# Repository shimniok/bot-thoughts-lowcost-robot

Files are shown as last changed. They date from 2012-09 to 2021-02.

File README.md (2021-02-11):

# bot-thoughts-lowcost-robot

Entry for 2012 African Robotics Network Challenge to build a $10, educational robot.



[Bot Thoughts Blog article](https://www.bot-thoughts.com/2012/09/entry-for-afron-10-dollar-robot-design.html)

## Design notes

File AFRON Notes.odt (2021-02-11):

Main issues:

Board assembly astronomically expensive, PTH self assembly may be the only option here. Even so have to have some level of SMT assembly for the motor drivers.

Servo work on 2xAA ? (2v – 3V) ? 3V=Yes, 2V=Untested

LiPo or AA (Alkaline or NiMH)?

Where to mount battery?

Ongoing cost of batteries (AA's are cheap but... not renewable)

Where to put sensors? Separate board = more $, mounting?? – chassis-board may be best?

3rd wheel steer bracket?

I don't have motor drivers prototyped

All the little extras are “nickle and dime”-ing this thing to $30

Test MiniBloq on 8mhz version

I'm out of money and time :)

Resolved

Will servo work on Lipo? ~3.7V? YES

Prototyped Arduino at Lipo/AA power, 4MHz (could do 8mhz with LiPo)

On-board LiPo charger or off-board? Off-board, but motor system could be its own charger; need to redirect power to charger board somehow.

On-board USB or off-board? (off-board, but could have ftdi / AVRISP shield and later revision could use mega32u4

AA requires 4MHz (5.333MHz @ 2V, 6.6667MHz @ 2.2V, 8MHz @ 2.4V)

LiPo can do 8MHz; change of MHz requires change to bootloader (can I get around this?)

Cost of wheels – Options: cardboard, bottle tops, cheap toy wheels

I don't have minibloq software going

I don't actually have the designed motor/gearbox yet

Features

Stackable headers for shields. Small size shields for low cost diy, hacking, low cost shield options for expanding capabilities

Built-in LEDs/Phototrans/Sensors can be disabled for use with shield

DIY solder assembly, secondary students can assemble for primary; benefit of lower cost plus gaining education (at some point you run out of people to pass robots down to though)

Arduino compatible

With booster circuit, can run with MiniBloq, either on regular laptop or OLPC laptop

Assembly Instructions

Summary

Highlights of board, features

Online documentation

Disable all phototransistor/LEDs : cut the power trace

Disable individual phototrans pins but cutting those traces

Support AA or 3.7V 1S Lipo?!

1. A high-level description of your robot design with total cost (for one prototype unit; see point 7

regarding volume pricing).

• Include in your description an indication of whether your robot is designed to be built from

scratch by the user, or mass manufactured and supplied as a kit to the user

• Some robots might have required accessories (e.g. a tool for downloading programs to the

robot) that can be shared by multiple robots in a classroom. If applicable, include such a

tool in the cost for a single robot, but also specify whether it can be shared by multiple

robots, thus bringing down the overall deployment cost for a classroom.

2. A description of the educational applications and possible resources.

• For example, what science and technology concepts or skills can your robot help students

learn?

3. A list of parts, their sources (include URLs if applicable), availability, and their prices.

• Note that salvaged parts are allowed, if these salvaged parts are commonly available in

your particular context. Think of this list of parts as the starting point if someone in a

similar context to you wanted to reproduce your robot.

• Note also that your parts list should be complete, including things like required adhesive,

screws etc.

• Your parts list should include any consumables (e.g. batteries) and their associated cost

and replacement frequency. This is a caution to think of sustainability.

4. A list of other tools and equipment needed to create your robot and estimated prices

5. Relevant drawings with dimensions.

• These may be CAD drawings, particularly for machined parts, but they may also be hand-

drawn

6. Step-by-step instructions for creating your robot

7. [Optional] If your robot can be mass manufactured, you can present an analysis of how costs

would scale with quantity.

8. Software, if any. All software must be available open-source.

9. A description of any actual experiments conducted

10. Pictures of your robot, if any.

11. Videos of your robot in action, if any.

• These videos should highlight key capabilities such as its ability to respond autonomously

to its environment.

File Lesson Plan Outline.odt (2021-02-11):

Robotics Lesson Plan Outline

I. Basic Electronics and Switches
  A. Electricity intro
    i. Batteries
    ii. Circuit
    iii. LED
    iv. Switch(?)
    v. Resistor(?)
  B. (Opt.) Solder components on board (assembled robots to primary edu)
  C. Wire up sensor switch(?)
  D. Load demo program (light LED when switch closed)
II. Motors and gears
  A. Force and Distance
    i. Leverage
    ii. Pulleys
  B. Gear reduction
    i. Leverage, torque
    ii. RPM, Formulas
      a. Calculate for our robot
    iii. Load demo motor driver
      a. RPM with motor out of case
      b. Demo wheel rpm with motor in
III. Simple programming with Minibloq
  A. Turn on LED
  B. Turn on LED with switch(?)
IV. Line following with Infrared Light
  A. Light spectrum
  B. Infrared light
  C. LED review
  D. Phototransistors

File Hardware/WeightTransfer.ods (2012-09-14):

AFRON ROBOT WEIGHT TRANSFER DATA
Inner | Outer | Total | Inner % | Outer %
28 | 34 | 62 | 45% | 55%
22 | 38 | 60 | 37% | 63%
20 | 40 | 60 | 33% | 67%
26 | 38 | 64 | 41% | 59%

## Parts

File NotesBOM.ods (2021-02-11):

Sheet: Sheet1
Mass Production Cost Analysis
Summary | Description | Price ($) / Pack | Qty / Pack | Qty / Robot | Packs / 1000 | Subtotal @ 1000 | Price Ea. @ 1000 | Source
Locomotion
Gearbox | UCTronics 6V Dual axle brush DC Gear Motor & boxes | 2.9 | 1 | 1 | 1000 | $2,900.00 | $2.90
Drive wheels | 20x8x2 | 26.32 | 100 | 2 | 20 | $526.40 | $0.26 | http://www.aliexpress.com/item/20x8x2mm-Academic-Model-Small-Wheels-Plastic-DIY-Toys-Hobbies-Parts-and-Accessories/517602128.html
Axles | 2mm x 20mm axle | 7.59 | 80 | 2 | 25 | $189.75 | $0.09 | http://www.aliexpress.com/item/20mm-2mm-Toys-axle-Shaft-axis/582061924.html
Rear steer wheels | Fingerboard wheels (400 pack) | 20 | 400 | 2 | 5 | $100.00 | $0.05 | http://www.aliexpress.com/item/400pcs-10-Colors-Wheel-For-Fingerboard-Mini-Skateboard-Finger-board/447293443.html
Rear steer bracket | Fingerboard Truck, screws, nuts, red | 80 | 200 | 1 | 5 | $400.00 | $0.40 | http://www.aliexpress.com/item/wholesale-200pcs-finger-skateboard-truck-fingerboards-truck-29-mm-wide-truck-fee-shipping-by-UPS-EMS/446988459.html
Bracket | Servo mount bracket | 0.03 | 1 | 1 | 1000 | $30.00 | $0.03 | http://www.cshardware.com/steel-brackets/15-3412.asp
Servo | TowerPro SG90, 9g servo | 177.38 | 100 | 1 | 10 | $1,773.80 | $1.77 | http://www.aliexpress.com/item/fast-shipping-100pcs-Tower-Pro-9g-micro-servo-for-6CH-rc-helcopter-kds-esky-align-helicopter/555525944.html
Sensors
3mm 940nm IR LED | Kingbright WP710A10F3C | 0.104 | 1 | 4 | 4000 | $416.00 | $0.10 | Digi-Key
3mm 940nm IR PhotoTrans | LTR-4206E | 0.09 | 1 | 4 | 4000 | $360.00 | $0.09 | Digi-Key
Heat Shrink | HEATSHRINK LOW TEMP 1/8" 60' BLK | 23.18 | 720 | 3 | 5 | $115.90 | $0.04 | Digi-Key
Main Board
MCU | ATmega328P-PU | 1.7628 | 1 | 1 | 1000 | $1,762.80 | $1.76 | Digi-Key
Driver IC | SI1563EDH-T1-E3 1.8V SOT-363 | 0.1919 | 1 | 2 | 2000 | $383.80 | $0.19 | Digi-Key
Crystal resonator | Murata CSTLS8M00G53-B0 | 0.1234 | 1 | 1 | 1000 | $123.42 | $0.12 | Digi-Key
LED | 3mm LED, water clear, green | 0.0481 | 1 | 1 | 1000 | $48.10 | $0.05 | Digi-Key
Motor capacitor | Vishay K103K10X7RF5UH5, CAP CER 10000PF 50V 10% RADIAL | 0.0303 | 1 | 1 | 1000 | $30.30 | $0.03 | Digi-Key
0.1uF Bypass capacitor | Vishay K104K10X7RF5UH5, CAP CER 0.1UF 50V 10% RADIAL | 0.0369 | 1 | 3 | 3000 | $110.70 | $0.04 | Digi-Key
100uF capacitor | Kemet ESK107M010AC3AA | 0.02954 | 1 | 1 | 1000 | $29.54 | $0.03 | Digi-Key
100 ohm resistor | Stackpole CF18JT100R | 0.00992 | 1 | 5
Description | Price @ 1 | Price @ 100 | Price @ 1000 | Qty | Subtotal | Option 1 | Option 2 | Option 2 | Option 3 | Drivetrain
UCTronics 6V Dual axle brush DC Gear Motor & boxes | $2.90 |  |  | 1 | $2.90 | $2.90 | $2.90 | $2.90
Dollar store | $1.00 | $1.00 | $1.00 | 1 | $1.00 | $1.00
CDR for wheel | $0.16 | $0.16 | $0.16 | 2 | $0.32 |  |  | $0.32
AliExpress | $0.44 | $0.40 | $0.40 | 2 | $0.88 |  | $0.88
AliExpress | $0.40 | $0.36 | $0.36 | 1 | $0.40 |  | $0.40
K&S, 2mm dia, unknown length, 4-pack | $1.79 |  |  | 1 | $1.79
FDS9934C 6.5A/-5A SO-8 | $0.91 | $0.61 | $0.36 | 2 | $1.82 | $1.82 | $1.82 | $1.82
20-pack | $0.59 | $0.59 | $0.59 | 1 | $0.59 |  |  |  | $0.59
Woodwoorks 1" bead | $0.20 | $0.20 | $0.20 | 2 | $0.40 |  |  |  | $0.40
Woodworks 3/8" hardwood dowel | $1.19 | $1.19 | $1.19 | 1 | $1.19 |  |  |  | $0.50
EXI S1123 9G Micro Servo | $3.00 |  |  | 1 | $3.00 | $3.00 | $3.00 | $3.00 | $3.00
 |  |  |  |  |  | $8.72 | $9.00 | $8.04 | $4.49 | TOTALS
 |  |  |  |  |  |  |  |  |  | Sensors
 | $0.87 | $0.58 | $0.43 | 2 | $1.74 |  |  | $1.74
 | $0.93 |  |  | 2 | $1.86 |  |  |  | $1.86
 | $0.26 | $0.14 | $0.10 | 3 | $0.78 | $0.78 | $0.78
 | $0.38 | $0.18 | $0.09 | 3 | $1.14 | $1.14
Vishay TSOP34838 | $1.14 |  |  | 1 | $1.14 |  | $1.14
K&S 0.015 25pk | $0.42 |  |  | 1 | $0.42 | $0.42 | $0.42 | $0.42
 |  |  |  |  |  | $1.92 | $1.92 | $1.74 | $1.86 | TOTALS
 |  |  |  |  |  |  |  |  |  | MCU, board, USB, Batt
Digikey price | $1.92 | $1.35 | $1.20 | 1 | $1.92
Appx price | $1.20 | $0.76 | $0.67 | 1 | $1.20 |  |  |  | $1.20
Appx price | $3.50 |  |  | 1 | $3.50
Appx price | $3.05 | $1.92 | $1.70 | 1 | $3.05 | $3.05 |  |  |  |  | Note: MiniBloq only supports ATmega328/168 and ATtiny25/45/85
Digikey | $6.04 | $3.37 | $3.37 | 1 | $6.04 |  |  | $6.04
Appx price | $3.80 |  |  | 1 | $3.80 |  | $3.80
FTDI chip (digikey) | $2.38 | $1.79 | $1.58 | 1 | $2.38 | $2.38 |  |  | $2.38
FT232RL, Digikey | $4.50 | $3.65 | $2.85 | 1 | $4.50
digikey | $0.68 | $0.55 | $0.55 | 1 | $0.68 | $0.68 | $0.68 | $0.68 | $0.68
3 x 3mm / #2
Sparkfun | $18.00 |  |  | 1 | $18.00
various sources | $3.00 |  |  | 1 | $3.00 | $3.00 | $3.00 | $3.00 | $3.00
SFE | $10.00
asdf | $0.15 | $0.10 | $0.08 | 2 | $0.30 | $0.30 | $0.30 | $0.30 | $0.30
Lipo, 1S, 210mAH 15C | $1.77 |  |  | 1 | $1.77
 |  |  |  |  |  | $9.41 | $7.78 | $10.02 | $7.56 | TOTALS
 |  |  |  |  |  |  |  | $20.05 |  | TOTALS
LB1836M; 1.8V motor, 2.5V logic, 1A | $4.61 |  |  | 1 | $4.61
sn754410 appx price | $2.30 |  |  | 1 | $2.30
4.5V-18V TC4427A appx price | $1.50 |  |  | 1 | $1.50
Victor mousetrap, amazon, 4-pack | $1.16 |  |  | 2 | $2.32
72-pack | $0.54 |  |  | 72 | $38.95
20-pack | $0.59 |  |  | 20 | $11.78
Car Robot Plastic Tire Wheel + DC Gear Motor (ebay) | $4.19 |  |  | 2 | $8.38
Car Robot Plastic Tire Wheel + DC Gear Motor (ebay) | $2.95 | $2.95 | $2.95 | 2 | $5.90
11 pc plastic | $2.50 |  |  | 1 | $2.50
1230 Mini Hi Torque motor | $1.70 |  |  | 2 | $3.40
Woodworks 2.5" flat wood wheel | $0.58 |  |  | 2 | $1.15
Woodwoorks 1" bead | $0.20 |  |  | 2 | $0.40
Woodworks 2" flat wood wheel | $0.30 |  |  | 2 | $0.60 |  |  |  | $0.60
Surplus Elect Sales 3V hobby motor | $0.99 |  |  | 1 | $0.99
5V 7200 rpm dc motor | $0.65 |  |  | 2 | $1.30
ULTRALAST UL40AAVP 40-pack AA Alkaline Batteries (newegg) | $0.22 |  |  | 2 | $0.45
AA, cheapbatteries.com | $0.15 | $0.10 | $0.08 | 2 | $0.30
LB1838M, stepper only? low voltage | $3.11 |  |  | 1 | $3.11
BD6211 8SOIC | $3.24 |  |  | 1 | $3.24
DRV8830, 10MSOP | $2.71 |  |  | 1 | $2.71
ZXMHC3F381 H-bridge | $1.08 |  |  | 1 | $1.08
4.5V+ (see Pololu Baby-O 328P, only carried at DigiKey) | $2.03 |  |  | 1 | $2.03 |  |  | $2.03 | $2.03
DRV8837, single H-bridge, DSG pkg | $1.62 | $1.13 | $0.70 | 1 | $1.62 | $1.62 | $1.62
2V - 11V; See Pololu DRV8835; Ti part, DigiKey best price; DFN pkg | $2.23 | $1.62 | $1.04 | 1 | $2.23 |  | $2.23
DigiKey | $1.94 | $1.08 | $1.08
DigiKey (appx) | $4.80
Pair | $9.95
FDC6327C 2.5V 2.7A/-1.9A SOT-6 | $0.51 | $0.32 | $0.18 | 2 | $1.02
SI1563EDH-T1-E3 1.8V SOT-363 | $0.56 | $0.33 | $0.19 | 2 | $1.12
NTHC5513 3.9A/-3.0A ChipFET | $0.64 | $0.40 | $0.23 | 2 | $1.28
NTHD3102CT 5.5A/-4.2A ChipFET | $0.68 | $0.46 | $0.27 | 2 | $1.36
SI519EDJ 4.5A/-4.5A PowerPak 8 | $0.74 | $0.45 | $0.26 | 2 | $1.48
Si3590DV 2A/-1.3A TSOP-6 | $0.79 | $0.48 | $0.27 | 2 | $1.58
DMC2020USD 7.8A/-6.3A SO-8 | $0.82 | $0.56 | $0.33 | 2 | $1.64
FDS9934C 6.5A/-5A SO-8 | $0.91 | $0.61 | $0.36 | 2 | $1.82 | $1.82 | $1.82 | $1.82
NTHD3102CT 5.5A/-4.2A ChipFET | $0.68 | $0.46 | $0.27 | 2 | $1.36 | $1.36 | $1.36 | $1.36
SFE | $10.00
SFE | $14.95
various | $3.00
 | $3.30 |  |  |  |  |  |  |  |  |  | http://www.aliexpress.com/item/20W-110V-220V-Mini-Electric-Heating-Hot-Melt-Glue-Gun-Crafts-Repair-Tool-Professional-US-Plug/487529881.html
 | $0.18 |  |  |  |  |  |  |  |  |  | http://www.aliexpress.com/item/free-shipping-7-100mm-Home-essential-universal-hot-melt-tape-hot-melt-glue-stick-100pcs-alot/607201791.html
PCBFabExpress |  | $25.70 | $18.75 |  |  |  |  |  |  |  | http://www.pcbfabexpress.com/assembly/as_quotemain_test.jsp
Screaming Circuits |  | $19.31 | $18.82 |  |  |  |  |  |  |  | http://www.screamingcircuits.com
MyroPCB |  | $3.53 |  |  |  |  |  |  |  |  | http://www.myropcb.com/online-quote/pcba-prototype-quote/
Hakko 503F-V12ED 60 Watt Heavy Duty Solder Iron | $11.92 |  |  |  |  |  |  |  |  |  | http://www.frys.com/product/249084?source=googleps&gclid=CKK6hK3Dq7ICFSVgMgod-2UAXQ
Weller SP23L 25 Watt Marksman Solder Iron | $9.97 |  |  |  |  |  |  |  |  |  | http://www.frys.com/product/2818734?site=sr:SEARCH:MAIN_RSLT_PG
220V 60W | $6.88 |  |  |  |  |  |  |  |  |  | http://www.ebay.com/itm/AC-220V-40-Watt-Soldering-Iron-Dissolved-solder-Tip-Electronic-Welding-TOOL-/140811445683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
220V 40W | $3.20 |  |  |  |  |  |  |  |  |  | http://www.aliexpress.com/item/Fast-Heating-Welding-Soldering-Iron-Tool-Electronic-PC-40W-220V-SHT-0075/622355190.html
110/220 25W-60W | $14.99 |  |  |  |  |  |  |  |  |  | http://www.aliexpress.com/item/110V-220V-Adjustable-Gun-Welding-Soldering-Solder-Iron-Handle-Tool-For-933-Station-Heat-Pencil-25W/572357938.html
FEITA 30W 40W 60W 80W electric solder Irons with ROHS SGS | $5.85 |  |  |  |  |  |  |  |  |  | http://www.aliexpress.com/item/30W-40W-60W-80W-electric-welder-Irons/434076066.html

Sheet: Sheet2
 |  |  |  |  |  | http://www.aliexpress.com/item/4-5-inch-besk-pliers-VK-031/460402968.html
Steer Wheel Bracket | Brass, e-machine shop | $1.92 |  | $1.96 | $1.06
Steer Wheel Bracket | inj molded nylon | $1.04 |  | $4.74 | $1.04
Steer Wheel Bracket | 5/8" square bead, 1/4" hole | $0.11 | 1 | $0.11 | $0.08 | http://www.craftparts.com/square-beads-hole-p-1018.html
Steer Wheel | 1" wood slab wheel | $0.15 | 2 | $0.15 | $0.12 | http://www.craftparts.com/flat-wood-slab-wheels-thick-p-590.html
Steer axle | 1-3/8" x 1/4" peg | $0.05 | 2 | $0.09 | $0.08 | http://www.craftparts.com/138-axle-pegs-1564-tenon-p-851.html
Steer Wheel | dia unknown | $0.27 |  |  |  | http://www.aliexpress.com/item/100pcs-DIY-accessories-Plastic-toy-car-wheels-3CM/450620588.html
Wheel | 30x9x1.9 | $0.70 |  | $0.60 |  | http://www.aliexpress.com/item/Free-shipping-30-9-1-9mm-Plastic-wheel-DIY-handmade-Model-accessories-Toy-car-wheels/574791665.html
Wheel | 18x6.5x2 | $0.34 |  | $0.34 | $0.30 | http://www.aliexpress.com/item/18x6-5x2mm-Academic-Model-Small-Plastic-Toy-Car-Wheels-DIY-Hobbies-Parts-and-Accessories/517605266.html
Wheel | 20x8x2 | $0.29 |  |  |  | http://www.aliexpress.com/item/20x8x2mm-Academic-Model-Small-Wheels-Plastic-DIY-Toys-Hobbies-Parts-and-Accessories/517602128.html
Wheel (clear) | 64x2.5mm | $0.56 |  |  |  | http://www.aliexpress.com/item/30pcs-DIY-Accessories-Plastic-toy-car-wheels-64MM-Remote-control-car-wheels/452423232.html
Wheel | 46x22x2 | $0.29 |  |  |  | http://www.aliexpress.com/item/50pcs-DIY-accessories-Plastic-toy-car-wheels-4-6CM/450625545.html
Wheel | 45x18x3 | $0.45 |  |  |  | http://www.aliexpress.com/item/45x18x3mm-Academic-Model-Small-Wheels-Plastic-DIY-Toys-Hobbies-Parts-and-Accessories/517593841.html
Wheel | 58x2.5 | $0.69 |  |  |  | http://www.aliexpress.com/item/toy-wheels-58mm-plastic-wheels-Shaft-Diameter-2-5mm-model-making-DIY-model-accessories-10-pcs/573590653.html
42mm Tires/Wheels 2mm | AliExpress | $0.19 | 3 | $0.57 | $0.57 | http://www.aliexpress.com/item/Free-Sipping-Toy-plastic-wheel-Technology-Small-Productions-DIY-Accessories-30mm-diameter-hole-2mm/591272358.html
Rear steer wheel | Fingerboard wheels (400) | $0.05 | 2 | $0.10 | $0.10 | http://www.aliexpress.com/item/400pcs-10-Colors-Wheel-For-Fingerboard-Mini-Skateboard-Finger-board/447293443.html
Rear steer wheel | Fingerboard bearing wheels | $0.24 | 2 | $0.48 | $0.48 | http://www.aliexpress.com/item/fingerboards-bearing-wheel-bearing-wheels-finger-skateboard-bearing-wheel-free-shipping/447735920.html
Rear steer bracket | Fingerboard Truck, screws, nuts, red | $0.43 | 1 | $0.43 | $0.43 | http://www.aliexpress.com/item/wholesale-200pcs-finger-skateboard-truck-fingerboards-truck-29-mm-wide-truck-fee-shipping-by-UPS-EMS/446988459.html
Bracket | Servo mount bracket | $0.05 | 1 | $0.05 | $0.05 | http://www.cshardware.com/steel-brackets/15-3412.asp
Steer wheel bracket | Wood square dowel | $0.32 | 1 | $0.32 | $0.32
Steer bracket, wheel | truck, wheels, nuts | $0.45 | 1 | $0.45 | $0.45 | http://www.ebay.com/itm/20-Trucks-40-Wheels-For-96mm-Fingerboard-Skateboard-Canadian-Maple-wooden-M19E-/110947473210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
2mm x 30mm axle | AliExpress | $0.20 | 1 | $0.20 | $0.20 | http://www.aliexpress.com/item/30mm-2mm-Toys-axle-Shaft-axis/582062768.html

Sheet: Sheet3
Drive axles | 2mm x 20mm axle | $0.20 | 2 | $0.40 | http://www.aliexpress.com/item/20mm-2mm-Toys-axle-Shaft-axis/582061924.html
Drive wheels | 20x8x2 | $0.29 | 2 | $0.58 | http://www.aliexpress.com/item/20x8x2mm-Academic-Model-Small-Wheels-Plastic-DIY-Toys-Hobbies-Parts-and-Accessories/517602128.html
Servo | AliExpress, bulk or HobbyPartz, one | $3.00 | 1 | $3.00 | http://www.aliexpress.com/item/fast-shipping-100pcs-Tower-Pro-9g-micro-servo-for-6CH-rc-helcopter-kds-esky-align-helicopter/555525944.html
 | UCTronics 6V Dual axle brush DC Gear Motor & boxes
Rear steer wheels | Fingerboard wheels (400) | $0.05 | 2 | $0.10 | http://www.aliexpress.com/item/400pcs-10-Colors-Wheel-For-Fingerboard-Mini-Skateboard-Finger-board/447293443.html
Rear steer bracket | Fingerboard Truck, screws, nuts, red | $0.43 | 1 | $0.43 | http://www.aliexpress.com/item/wholesale-200pcs-finger-skateboard-truck-fingerboards-truck-29-mm-wide-truck-fee-shipping-by-UPS-EMS/446988459.html
100 resistor | 1/8W similar to Stackpole CF18JT100R | $0.09 | 4 | $0.36
1K resistor | 1/8W similar to Stackpole CF18JT1K00 | $0.09 | 1 | $0.09
10K resistor | 1/8W similar to Stackpole CF18JT1M00 | $0.09 | 7 | $0.63
Motor driver | SI1563EDH-T1-E3 1.8V SOT-363 | $0.56 | 2 | $1.12
Motor Driver IC | Pololu DRV8835 breakout | $5.95 | 1 | $5.95
Charger |  | 9.95 |  |  | https://www.sparkfun.com/products/10217
Production battery | 3.7V 1S 600mAH, 2-pin JST | 2.73 |  |  | http://www.hobbyking.com/hobbyking/store/__20385__Turnigy_nano_tech_600mah_1S_35_70C_Lipo_Pack_Fits_Nine_Eagles_Solo_Pro_328_Eflite_MQX_120SR_.html
Production battery | 3.7V 1S 750mAH, 2-pin molex | 2.34 |  |  | http://www.hobbyking.com/hobbyking/store/__20386__Turnigy_nano_tech_750mah_1S_35_70C_Lipo_Pack_Fits_Nine_Eagles_Solo_Pro_180_.html

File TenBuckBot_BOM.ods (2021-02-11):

10 Dollar Robot Design Challenge
Bill of Materials
Prototype
Chassis |  | Qty 1
Wheels | Dollar store pull-back toy car | $1.00
Axles | See wheels
Chassis platform | Scrap cardboard | $0.00
Wood glue
Drive system | Solarbotics single-motor, dual axle gearbox | $5.95
Steering servo | EX1123 Servo | $3.00
Electronics
MCU | ATmega328P
Passives
Connectors
Sensors | 3 x IR LED |  |  | 3 x IR LED
 | 3 x IR Phototransistor |  |  | 3 x IR Phototransistor
Battery
Battery holder
Board | Assembly
 | Population
Accessories and Tools
programmer | FTDI breakout | $14.95 |  | FTDI cable (one per classroom) | $18.00
 | USB Cable | $3.00
Mass Produced Kit
 | Qty 1 | Qty 100 | Qty 1000
Scrap bottle tops, cardboard, CDs | $0.00 | $0.00 | $0.00
95mm x 2mm (AliExpress) | $0.40 | $0.36
Scrap cardboard, coke can, etc. | $0.00 | $0.00 | $0.00
UCTronics single-motor, dual axle gearbox | $2.90
Any 9g servo | $3.00
AliExpress: TP SG90 |  | $1.94

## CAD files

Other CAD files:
Electronics/AFRON_328_chassis.skp
Hardware/18mm Wheel.skp
Hardware/30mm Wheel.skp
Hardware/42mm Wheel.skp
Hardware/AFRON_Board.skp
Hardware/AFRON_Line_Sensor.skp
Hardware/Fingerboard.skp
Hardware/FingerboardRearSteer.skp
Hardware/PlasticServoMount.skp
Hardware/Servo Tower Pro Micro SG-90 with horns.skp
Hardware/SteerBracket.skp
Hardware/WoodPulley.skp
Hardware/WoodRearSteer.skp

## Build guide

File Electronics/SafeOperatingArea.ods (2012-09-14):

Clock | Clkdiv | Timer clock | OCR | Interrupt freq | Duty counter | PWM freq
8.00E+006 | 1 | 8000000 | 20 | 400000 | 64 | 6250
 |  |  |  | 5.00%
ATmega328P Safe Operating Area
rise | 4 | 10 | 6
run | 1.8 | 2.7 | 0.9 |  |  | V | F | rise | run | rise/run | Y-intercept
 |  |  | 6.6666666667 |  |  | 1.8 | 4
Volt | MHz |  |  |  |  | 2.7 | 10 | 6 | 0.9 | 6.6666666667 | -8
1.8 | 4.0 |  |  |  |  | 4.5 | 20 | 10 | 1.8 | 5.5555555556 | -5
1.9 | 4.7
2.0 | 5.3 |  | 4.5
2.1 | 6.0
2.2 | 6.7
2.3 | 7.3
2.4 | 8.0
2.5 | 8.7
2.6 | 9.3
2.7 | 10.0
2.8 | 10.6
2.9 | 11.1
3.0 | 11.7
3.1 | 12.2
3.2 | 12.8
3.3 | 13.3
3.4 | 13.9
3.5 | 14.4
3.6 | 15.0
3.7 | 15.6
3.8 | 16.0
3.9 | 16.7
4.0 | 17.2
4.1 | 17.8
4.2 | 18.3
4.3 | 18.9
4.4 | 19.4
4.5 | 20.0

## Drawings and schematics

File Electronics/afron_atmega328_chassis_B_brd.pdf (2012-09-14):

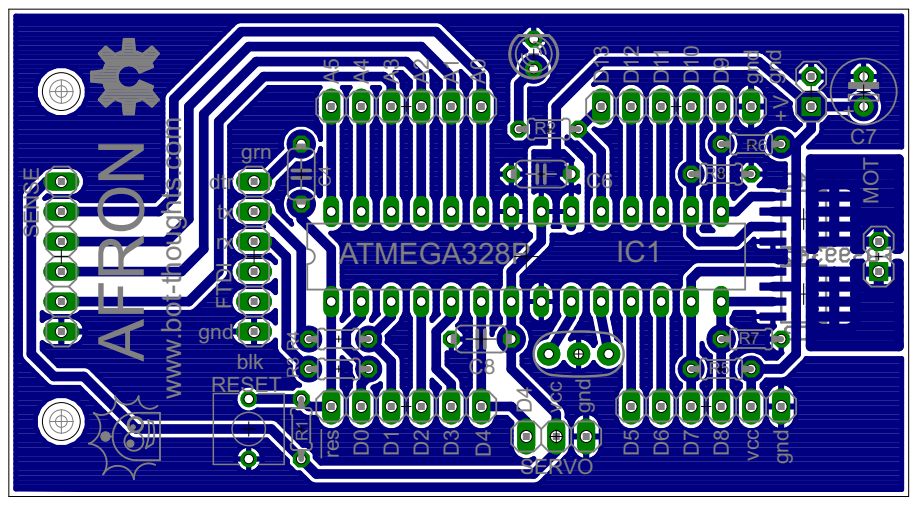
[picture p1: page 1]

AFRON www.bot-thoughts.com A3A4A5 vcc D2D3 gnd D4 vcc gnd D5D6 D11 D12 gnddtrtxrx A2A1A0 D7D8 D10 D9 D1D0 D13 RESET blkgrn D4 gnd res gnd R1 C6 R2 C4 R3 R4 R5 R6 R7 R8 IC1 C8 C7 +V FTDIATMEGA328P MOT SENSE SERVO

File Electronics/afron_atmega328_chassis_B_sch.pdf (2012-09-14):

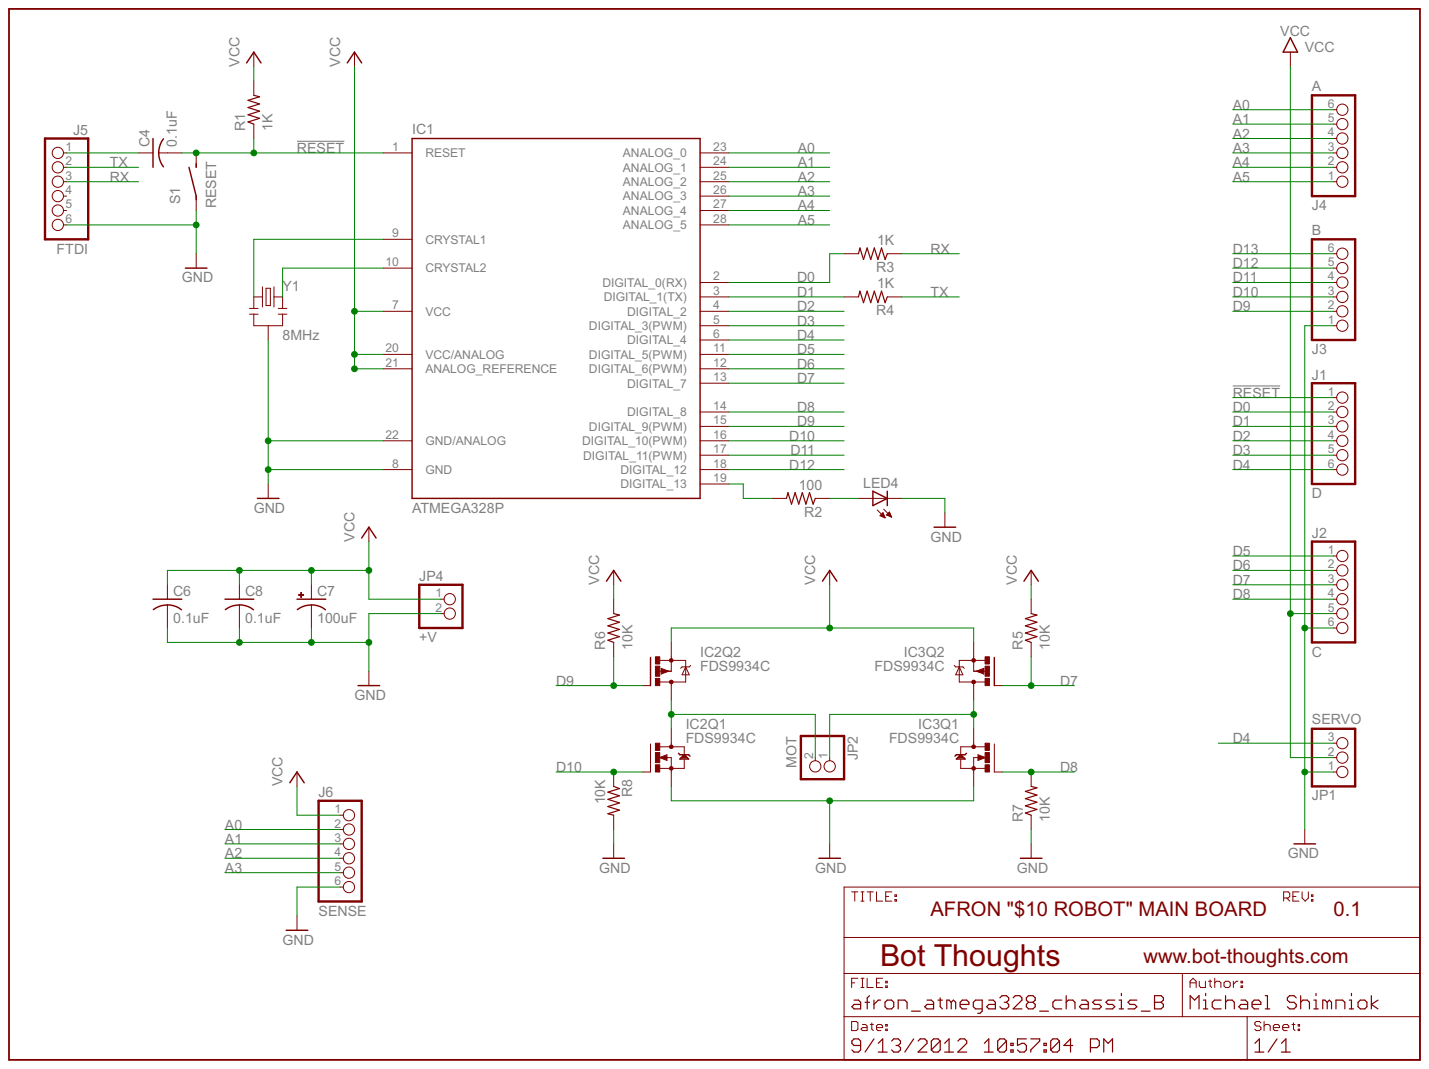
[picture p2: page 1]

20 | | 6 DIGITAL_3(PWM) 5 DIGITAL_2 D3

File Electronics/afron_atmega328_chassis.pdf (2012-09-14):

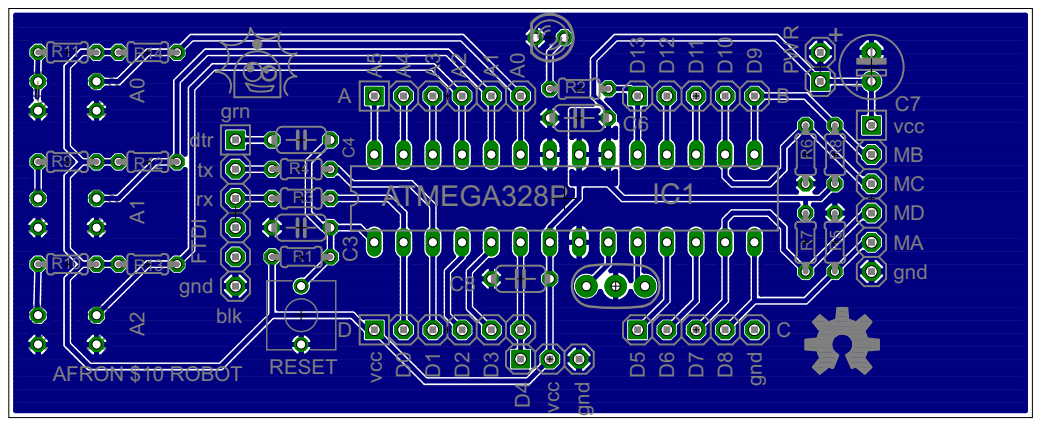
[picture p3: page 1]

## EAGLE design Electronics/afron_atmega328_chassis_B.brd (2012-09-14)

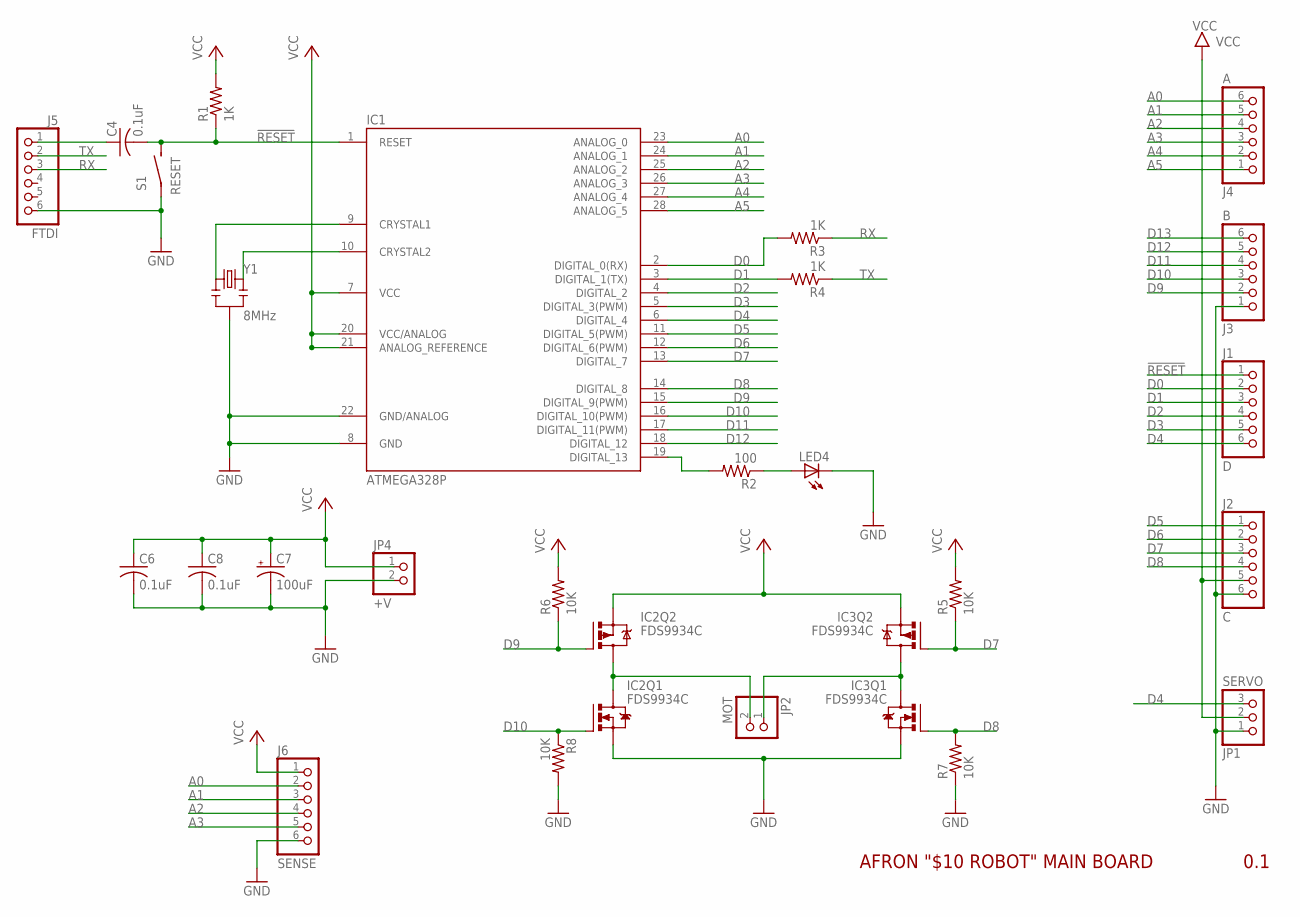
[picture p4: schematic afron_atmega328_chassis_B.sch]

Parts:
C4, C6, C8: 0.1uF; C050-024X044
C7: 100uF; E2,5-6
IC1: ATMEGA328P; DIL28-3
IC2, IC3: FDS9934C; SOIC8
J1: D; 1X06
J2: C; 1X06
J3: B; 1X06
J4: A; 1X06
J5: FTDI; 1X06
J6: SENSE; 1X06
JP1: SERVO; 1X03
JP2: MOT; 1X02-S
JP4: +V; 1X02-S
LED4: LED3MM
R1, R3, R4: 1K; 0204/5
R2: 100; 0204/5
R5, R6, R7, R8: 10K; 0204/5
S1: RESET; 6MMTACTILE
Y1: 8MHz; RESONATOR-PTH

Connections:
!RESET: C4.2, IC1.1 (RESET), J1.1, R1.1, S1.P$2 (S)
A0: IC1.23 (ANALOG_0), J4.6, J6.2
A1: IC1.24 (ANALOG_1), J4.5, J6.3
A2: IC1.25 (ANALOG_2), J4.4, J6.4
A3: IC1.26 (ANALOG_3), J4.3, J6.5
A4: IC1.27 (ANALOG_4), J4.2
A5: IC1.28 (ANALOG_5), J4.1
D0: IC1.2 (DIGITAL_0(RX)), J1.2, R3.2
D1: IC1.3 (DIGITAL_1(TX)), J1.3, R4.2
D2: IC1.4 (DIGITAL_2), J1.4
D3: IC1.5 (DIGITAL_3(PWM)), J1.5
D4: IC1.6 (DIGITAL_4), J1.6, JP1.3
D5: IC1.11 (DIGITAL_5(PWM)), J2.1
D6: IC1.12 (DIGITAL_6(PWM)), J2.2
D7: IC1.13 (DIGITAL_7), IC3.4 (G), J2.3, R5.1
D8: IC1.14 (DIGITAL_8), IC3.2 (G), J2.4, R7.2
D9: IC1.15 (DIGITAL_9(PWM)), IC2.4 (G), J3.2, R6.1
D10: IC1.16 (DIGITAL_10(PWM)), IC2.2 (G), J3.3, R8.1
D11: IC1.17 (DIGITAL_11(PWM)), J3.4
D12: IC1.18 (DIGITAL_12), J3.5
D13: IC1.19 (DIGITAL_13), J3.6, R2.2
GND: C6.2, C7.-, C8.2, IC1.8 (GND), IC1.22 (GND/ANALOG), IC2.1 (S), IC3.1 (S), J2.6, J3.1, J5.6, J6.6, JP1.1, JP4.2, LED4.K (C), R7.1, R8.2, S1.P$1, Y1.2
MA: IC2.5 (D), IC2.6 (D), IC2.7 (D), IC2.8 (D), JP2.2
MB: IC3.5 (D), IC3.6 (D), IC3.7 (D), IC3.8 (D), JP2.1
unnamed: IC1.9 (CRYSTAL1), Y1.1
unnamed: IC1.10 (CRYSTAL2), Y1.3
unnamed: C4.1, J5.1
unnamed: LED4.A, R2.1
RX: J5.3, R3.1
TX: J5.2, R4.1
VCC: C6.1, C7.+, C8.1, IC1.7 (VCC), IC1.20 (VCC/ANALOG), IC1.21 (ANALOG_REFERENCE), IC2.3 (S), IC3.3 (S), J2.5, J6.1, JP1.2, JP4.1, R1.2, R5.2, R6.2

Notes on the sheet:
AFRON "$10 ROBOT" MAIN BOARD
0.1

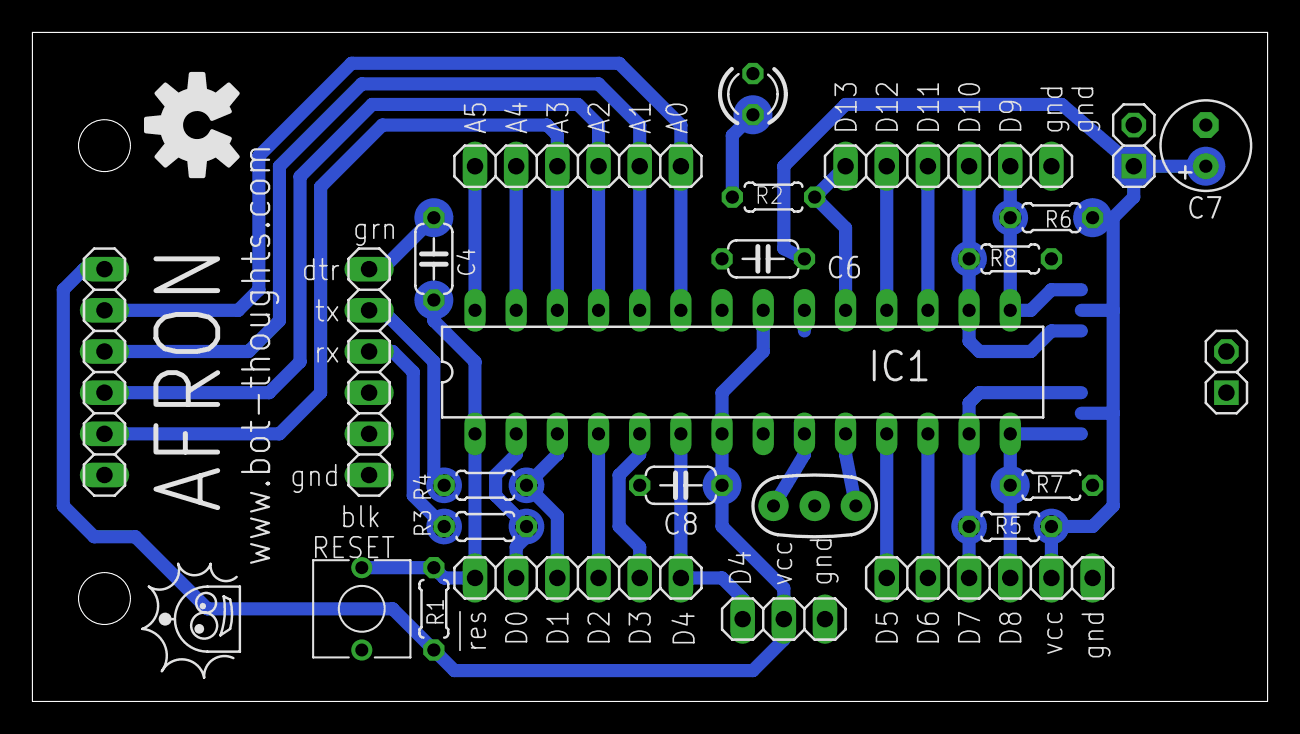
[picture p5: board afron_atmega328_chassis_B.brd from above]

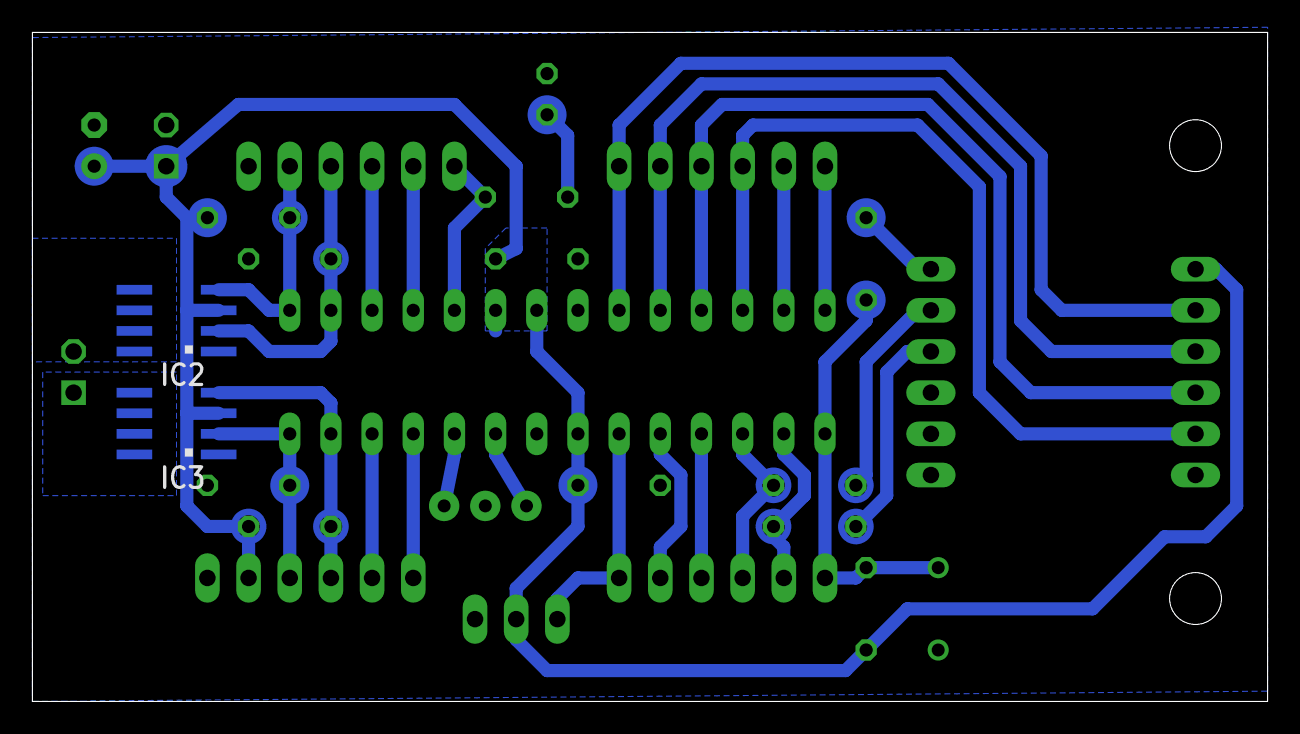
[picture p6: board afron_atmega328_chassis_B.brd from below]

Board: 2 copper layers, 76.2 x 41.3 mm, 27 parts (2 on the bottom side), 31 nets.

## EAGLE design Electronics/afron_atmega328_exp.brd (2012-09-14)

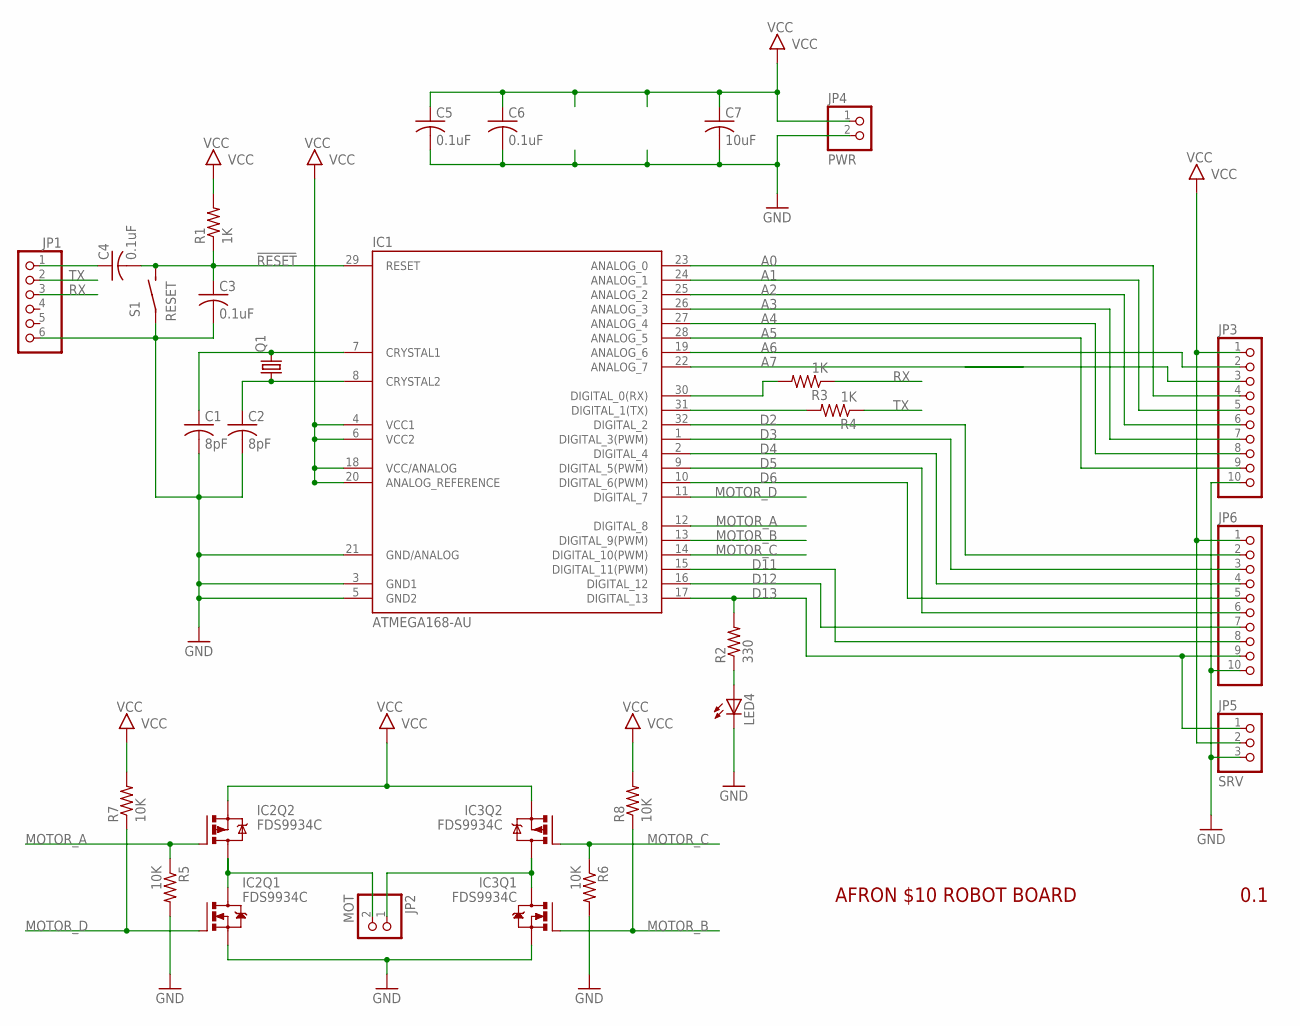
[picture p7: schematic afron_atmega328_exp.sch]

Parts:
C1, C2: 8pF; C0603
C3, C4, C5, C6: 0.1uF; C0603
C7: 10uF; C0805
IC1: ATMEGA168-AU; TQFP32-08
IC2, IC3: FDS9934C; SOIC8
JP1: PINHD-1X06_2.54-S; 1X06-S
JP2: MOT; 1X02-S
JP3, JP6: PINHD-1X10_2.54-S; 1X10-S
JP4: PWR; 1X02-S
JP5: SRV; 1X03-S
LED4: LEDSML0805; SML0805
Q1: CRYSTALNDK5X3; NDK_2PAD_5X3
R1, R3, R4: 1K; R0603
R2: 330; R0603
R5, R6, R7, R8: 10K; R0603
S1: RESET; 6MMTACTILE_RECT

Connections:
!RESET: C3.1, C4.2, IC1.29 (RESET), R1.1, S1.P$2 (S)
A0: IC1.23 (ANALOG_0), JP3.4
A1: IC1.24 (ANALOG_1), JP3.5
A2: IC1.25 (ANALOG_2), JP3.6
A3: IC1.26 (ANALOG_3), JP3.7
A4: IC1.27 (ANALOG_4), JP3.8
A5: IC1.28 (ANALOG_5), JP3.9
A6: IC1.19 (ANALOG_6), JP3.2
A7: IC1.22 (ANALOG_7), JP3.3
D2: IC1.32 (DIGITAL_2), JP6.2
D3: IC1.1 (DIGITAL_3(PWM)), JP6.3
D4: IC1.2 (DIGITAL_4), JP6.4
D5: IC1.9 (DIGITAL_5(PWM)), JP6.6
D6: IC1.10 (DIGITAL_6(PWM)), JP6.5
D11: IC1.15 (DIGITAL_11(PWM)), JP6.8
D12: IC1.16 (DIGITAL_12), JP6.7
D13: IC1.17 (DIGITAL_13), JP5.1, JP6.9, R2.2
GND: C1.2, C2.2, C5.2, C6.2, C7.2, IC1.3 (GND1), IC1.5 (GND2), IC1.21 (GND/ANALOG), IC2.1 (S), IC3.1 (S), JP1.6, JP3.10, JP4.2, JP5.3, JP6.10, LED4.C, R5.2, R6.2, S1.P$1
MA: IC2.5 (D), IC2.6 (D), IC2.7 (D), IC2.8 (D), JP2.2
MB: IC3.5 (D), IC3.6 (D), IC3.7 (D), IC3.8 (D), JP2.1
MOTOR_A: IC1.12 (DIGITAL_8), IC2.4 (G), R5.1
MOTOR_B: IC1.13 (DIGITAL_9(PWM)), IC3.2 (G), R8.1
MOTOR_C: IC1.14 (DIGITAL_10(PWM)), IC3.4 (G), R6.1
MOTOR_D: IC1.11 (DIGITAL_7), IC2.2 (G), R7.1
unnamed: C1.1, IC1.7 (CRYSTAL1), Q1.P$2 (2)
unnamed: C2.1, IC1.8 (CRYSTAL2), Q1.P$1 (1)
unnamed: C4.1, JP1.1
unnamed: LED4.A, R2.1
unnamed: IC1.31 (DIGITAL_1(TX)), R4.2
unnamed: IC1.30 (DIGITAL_0(RX)), R3.2
RX: JP1.3, R3.1
TX: JP1.2, R4.1
VCC: C5.1, C6.1, C7.1, IC1.4 (VCC1), IC1.6 (VCC2), IC1.18 (VCC/ANALOG), IC1.20 (ANALOG_REFERENCE), IC2.3 (S), IC3.3 (S), JP3.1, JP4.1, JP5.2, JP6.1, R1.2, R7.2, R8.2

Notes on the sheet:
AFRON $10 ROBOT BOARD
0.1

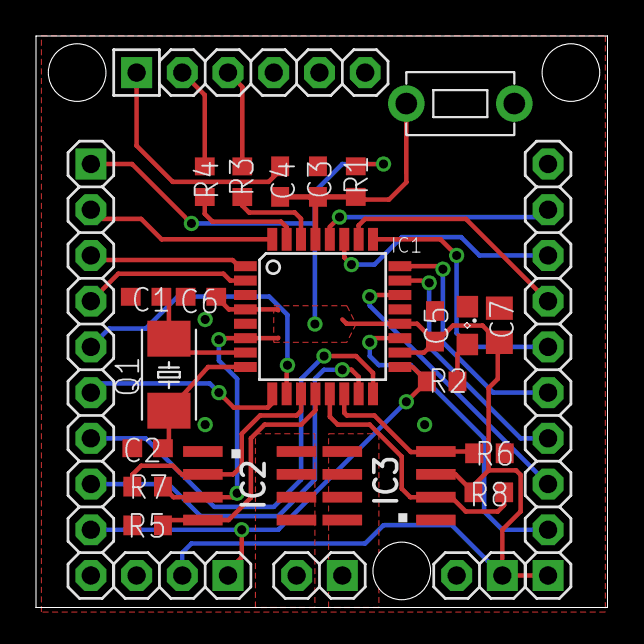
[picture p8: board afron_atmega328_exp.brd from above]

Board: 2 copper layers, 31.8 x 31.8 mm, 27 parts (0 on the bottom side), 33 nets.

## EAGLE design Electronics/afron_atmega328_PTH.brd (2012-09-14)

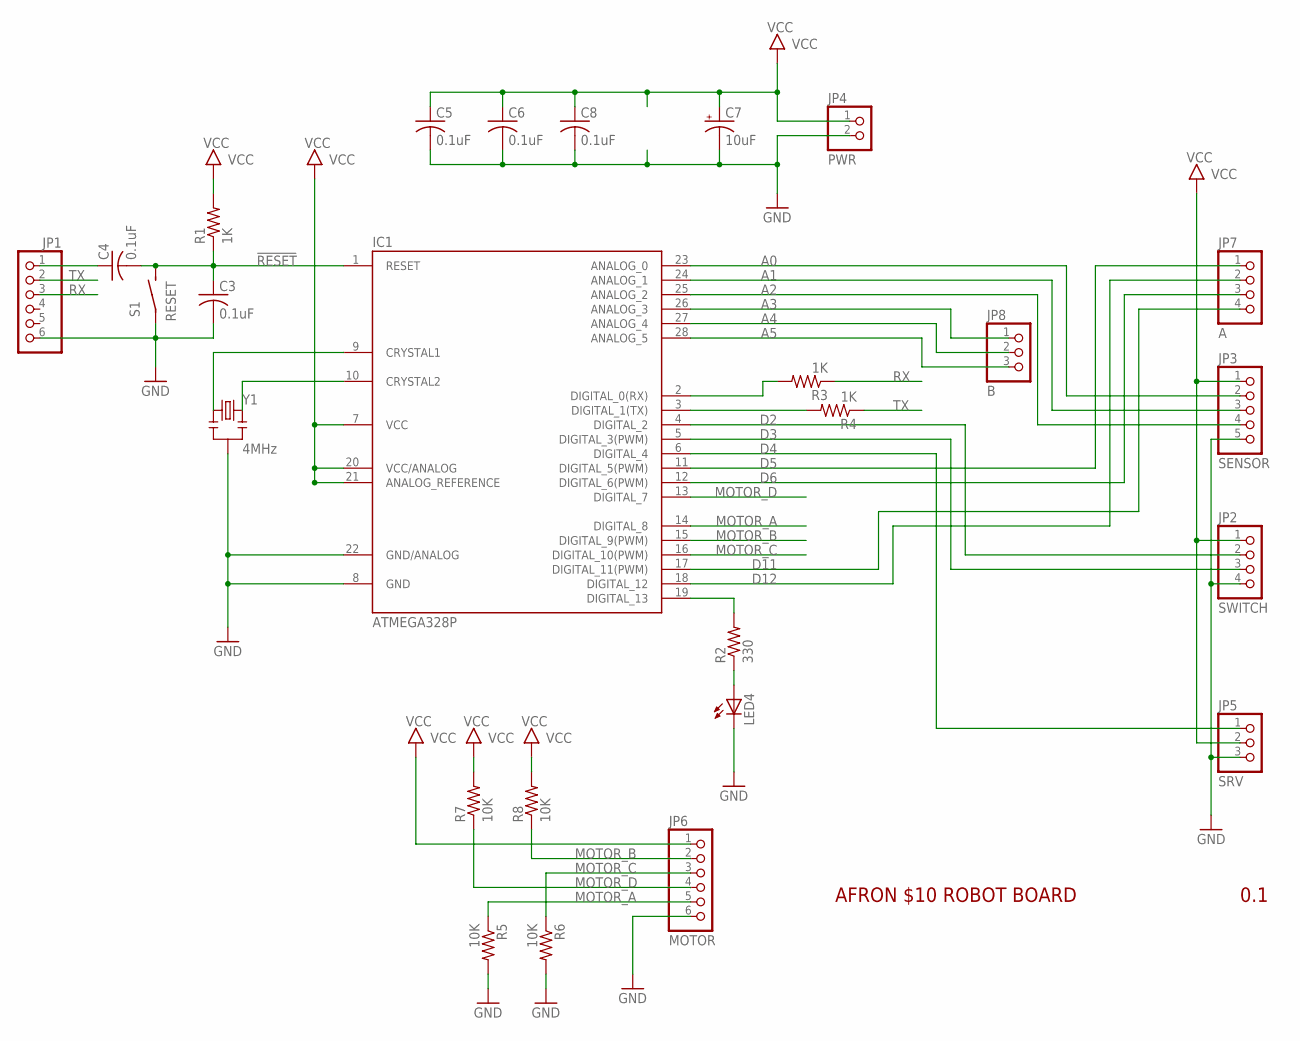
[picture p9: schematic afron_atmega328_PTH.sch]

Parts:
C3, C4, C6, C8: 0.1uF; C050-024X044
C5: 0.1uF; C0603
C7: 10uF; E2,5-6
IC1: ATMEGA328P; DIL28-3
JP1: PINHD-1X06_2.54-S; 1X06-S
JP2: SWITCH; 1X04-S
JP3: SENSOR; 1X05-S
JP4: PWR; 1X02-S
JP5: SRV; 1X03-S
JP6: MOTOR; 1X06-S
JP7: A; 1X04-S
JP8: B; 1X03-S
LED4: LED3MM
R1, R3, R4: 1K; 0204/5
R2: 330; 0204/5
R5, R6, R7, R8: 10K; R0603
S1: RESET; 6MMTACTILE
Y1: 4MHz; RESONATOR-PTH

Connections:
!RESET: C3.1, C4.2, IC1.1 (RESET), R1.1, S1.P$2 (S)
A0: IC1.23 (ANALOG_0), JP3.2
A1: IC1.24 (ANALOG_1), JP3.3
A2: IC1.25 (ANALOG_2), JP3.4
A3: IC1.26 (ANALOG_3), JP8.1
A4: IC1.27 (ANALOG_4), JP8.2
A5: IC1.28 (ANALOG_5), JP8.3
D2: IC1.4 (DIGITAL_2), JP2.2
D3: IC1.5 (DIGITAL_3(PWM)), JP2.3
D4: IC1.6 (DIGITAL_4), JP5.1
D5: IC1.11 (DIGITAL_5(PWM)), JP7.1
D6: IC1.12 (DIGITAL_6(PWM)), JP7.3
D11: IC1.17 (DIGITAL_11(PWM)), JP7.4
D12: IC1.18 (DIGITAL_12), JP7.2
D13: IC1.19 (DIGITAL_13), R2.2
GND: C3.2, C5.2, C6.2, C7.-, C8.2, IC1.8 (GND), IC1.22 (GND/ANALOG), JP1.6, JP2.4, JP3.5, JP4.2, JP5.3, JP6.6, LED4.K (C), R5.2, R6.2, S1.P$1, Y1.2
MOTOR_A: IC1.14 (DIGITAL_8), JP6.5, R5.1
MOTOR_B: IC1.15 (DIGITAL_9(PWM)), JP6.2, R8.1
MOTOR_C: IC1.16 (DIGITAL_10(PWM)), JP6.3, R6.1
MOTOR_D: IC1.13 (DIGITAL_7), JP6.4, R7.1
unnamed: IC1.9 (CRYSTAL1), Y1.1
unnamed: IC1.10 (CRYSTAL2), Y1.3
unnamed: C4.1, JP1.1
unnamed: LED4.A, R2.1
unnamed: IC1.3 (DIGITAL_1(TX)), R4.2
unnamed: IC1.2 (DIGITAL_0(RX)), R3.2
RX: JP1.3, R3.1
TX: JP1.2, R4.1
VCC: C5.1, C6.1, C7.+, C8.1, IC1.7 (VCC), IC1.20 (VCC/ANALOG), IC1.21 (ANALOG_REFERENCE), JP2.1, JP3.1, JP4.1, JP5.2, JP6.1, R1.2, R7.2, R8.2

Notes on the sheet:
AFRON $10 ROBOT BOARD
0.1

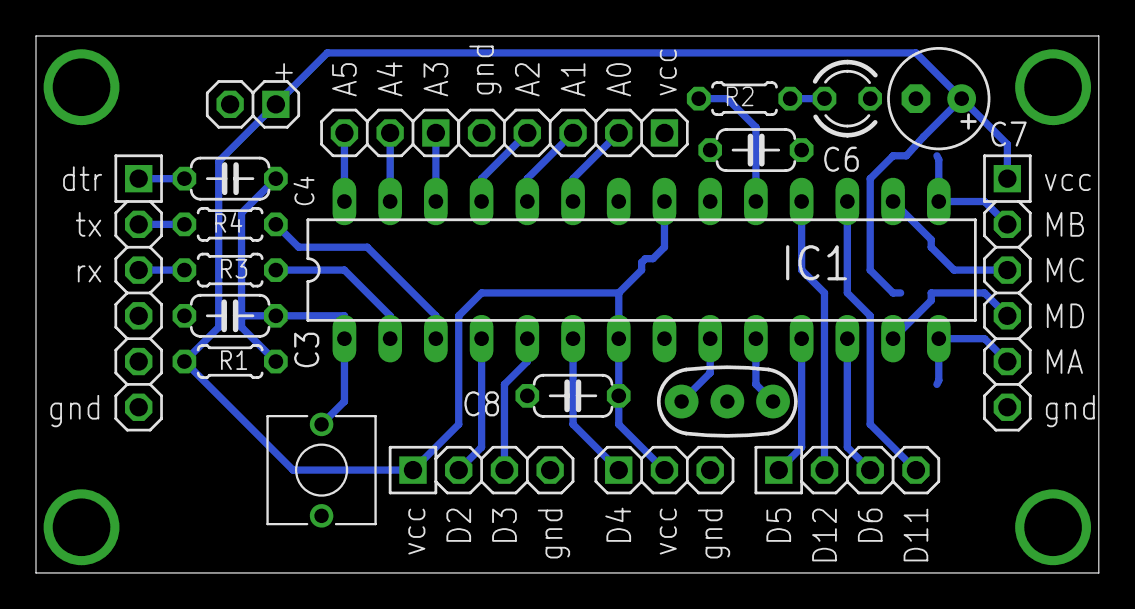
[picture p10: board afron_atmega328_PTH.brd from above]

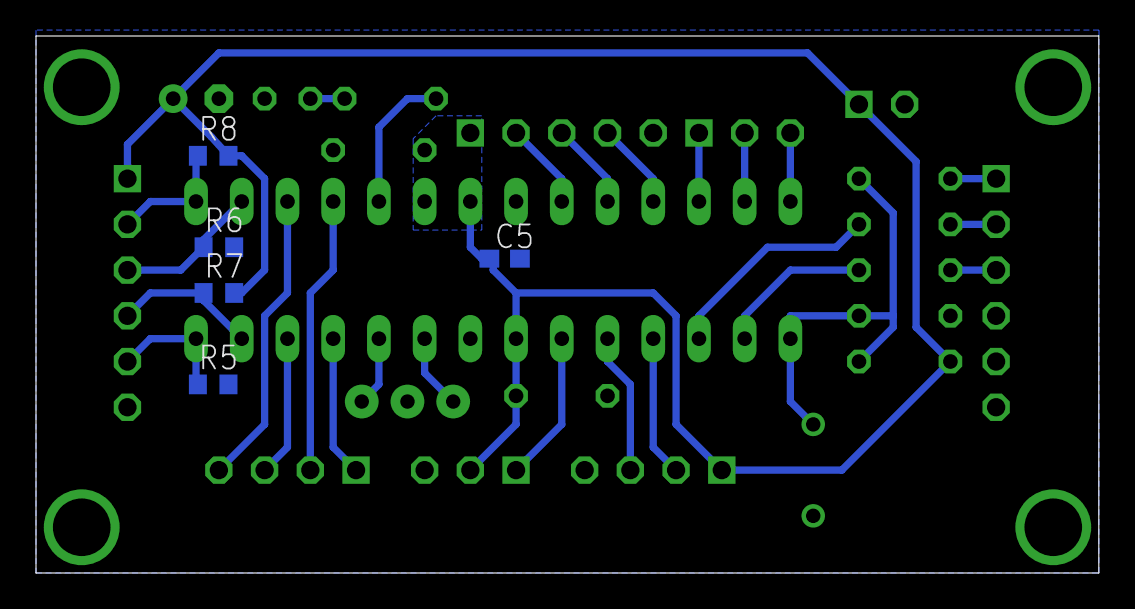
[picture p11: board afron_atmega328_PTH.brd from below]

Board: 2 copper layers, 59.0 x 29.8 mm, 26 parts (5 on the bottom side), 29 nets.

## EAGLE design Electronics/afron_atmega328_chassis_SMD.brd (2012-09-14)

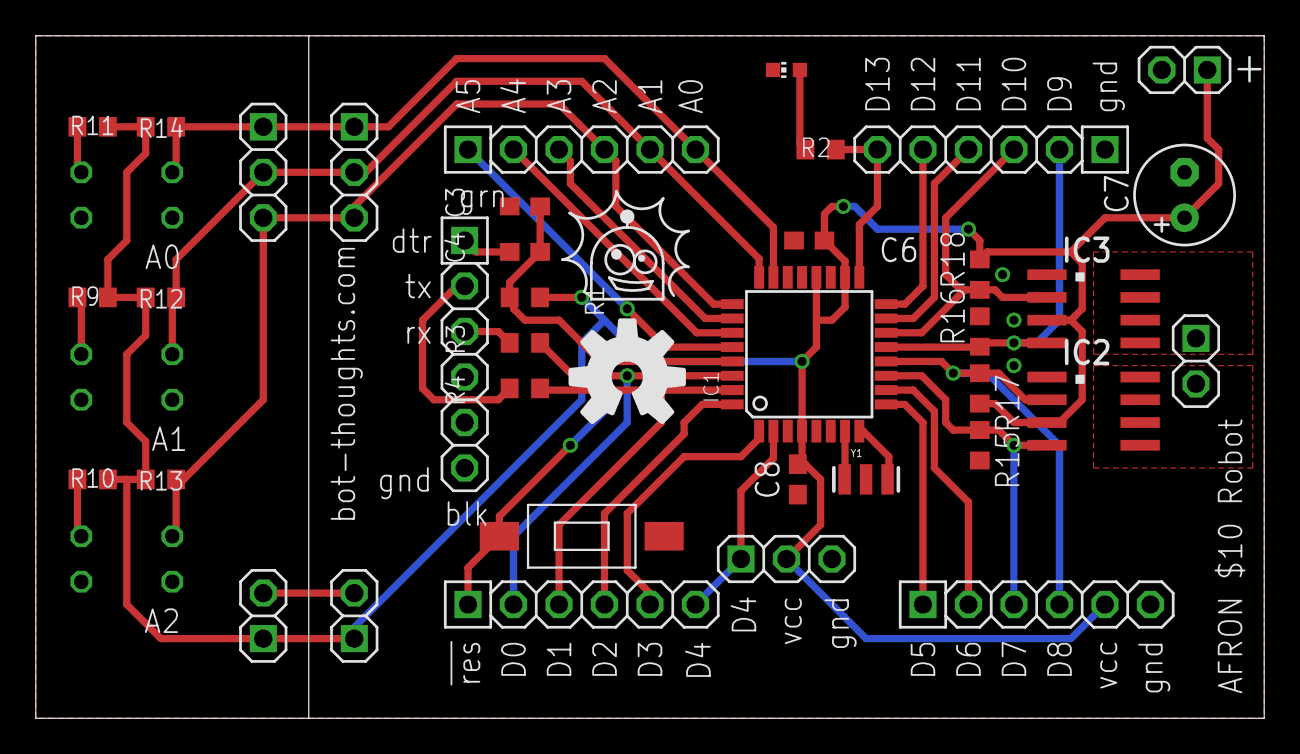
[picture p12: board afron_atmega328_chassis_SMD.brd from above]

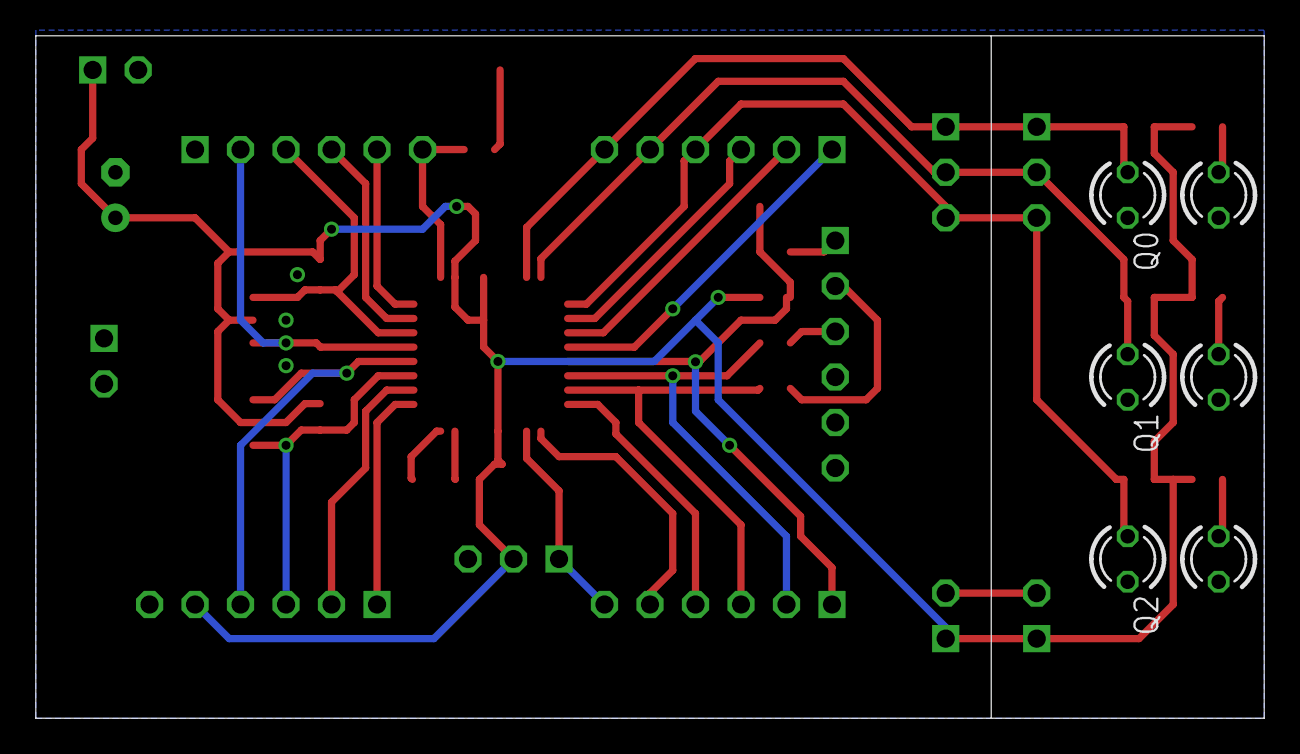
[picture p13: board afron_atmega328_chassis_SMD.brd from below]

Board: 2 copper layers, 68.6 x 38.1 mm, 43 parts (6 on the bottom side), 34 nets.

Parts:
C3, C4, C6, C8: 0.1uF; C0603
C7: 10uF; E2,5-6
IC1: ATMEGA168-AU; TQFP32-08
IC2, IC3: FDS9934C; SOIC8
J1: D; 1X06-S
J2: C; 1X06-S
J3: B; 1X06-S
J4: A; 1X06-S
J5: FTDI; 1X06-S
JP1, JP4, JP6: PWR; 1X02-S
JP2: MOT; 1X02-S
JP3, JP7: SENS; 1X03-S
JP5: SRV; 1X03-S
LED0, LED1, LED2: LED3MM
LED4: CHIP-LED0603
Q0, Q1, Q2: LED3MM
R1, R3, R4: 1K; R0603
R2, R9, R10, R11: 100; R0603
R12, R13, R14, R15, R16, R17, R18: 10K; R0603
S1: RESET; 6MMTACTTILE_RECT_SMD
Y1: 4MHz; RESONATOR-SMD

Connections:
!RESET: C3.1, C4.2, IC1.29, J1.1, R1.1, S1.P$2
A0: IC1.23, J4.6, JP3.1, JP7.1, Q0.A, R14.1
A1: IC1.24, J4.5, JP3.2, JP7.2, Q1.A, R12.1
A2: IC1.25, J4.4, JP3.3, JP7.3, Q2.A, R13.1
A3: IC1.26, J4.3
A4: IC1.27, J4.2
A5: IC1.28, J4.1
D0: IC1.30, J1.2, R3.2
D1: IC1.31, J1.3, R4.2
D2: IC1.32, J1.4
D3: IC1.1, J1.5
D4: IC1.2, J1.6, JP5.1
D5: IC1.9, J2.1
D6: IC1.10, J2.2
D7: IC1.11, IC2.4, J2.3, R15.1
D8: IC1.12, IC2.2, J2.4, R17.1
D9: IC1.13, IC3.4, J3.2, R16.1
D10: IC1.14, IC3.2, J3.3, R18.1
D11: IC1.15, J3.4
D12: IC1.16, J3.5
D13: IC1.17, J3.6, R2.2
GND: C3.2, C6.2, C8.2, IC1.3, IC1.21, IC2.1, IC3.1, J2.6, J3.1, J5.6, JP1.2, JP4.2, JP5.3, JP6.2, LED0.K, LED1.K, LED2.K, LED4.C, Q0.K, Q1.K, Q2.K, R15.2, R16.2, S1.P$1, Y1.2
MA: IC2.5, IC2.6, IC2.7, IC2.8, JP2.2
MB: IC3.5, IC3.6, IC3.7, IC3.8, JP2.1
unnamed: LED0.A, R11.1
unnamed: IC1.7, Y1.1
unnamed: IC1.8, Y1.3
unnamed: C4.1, J5.1
unnamed: LED2.A, R10.1
unnamed: LED4.A, R2.1
unnamed: LED1.A, R9.1
RX: J5.3, R3.1
TX: J5.2, R4.1
VCC: C6.1, C8.1, IC1.4, IC1.18, IC1.20, IC2.3, IC3.3, J2.5, JP1.1, JP4.1, JP5.2, JP6.1, R1.2, R9.2, R10.2, R11.2, R12.2, R13.2, R14.2, R17.2, R18.2

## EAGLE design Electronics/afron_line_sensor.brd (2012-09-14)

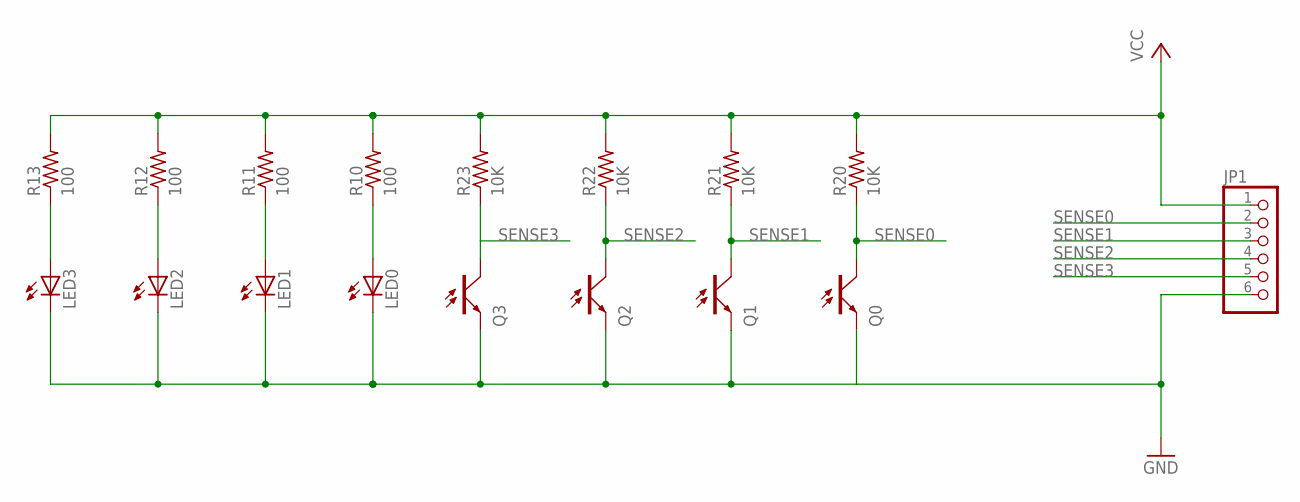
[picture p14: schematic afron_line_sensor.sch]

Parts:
JP1: PINHD-1X06_2.54; 1X06
LED0, LED1, LED2, LED3: LED3MM
Q0, Q1, Q2, Q3: PHOTOTRANSISTOR3MM; LED3MM
R10, R11, R12, R13: 100; 0204/5
R20, R21, R22, R23: 10K; 0204/5

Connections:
GND: JP1.6, LED0.K (C), LED1.K (C), LED2.K (C), LED3.K (C), Q0.K (C), Q1.K (C), Q2.K (C), Q3.K (C)
unnamed: LED0.A, R10.1
unnamed: LED2.A, R12.1
unnamed: LED3.A, R13.1
unnamed: LED1.A, R11.1
SENSE0: JP1.2, Q0.A, R20.1
SENSE1: JP1.3, Q1.A, R21.1
SENSE2: JP1.4, Q2.A, R22.1
SENSE3: JP1.5, Q3.A, R23.1
VCC: JP1.1, R10.2, R11.2, R12.2, R13.2, R20.2, R21.2, R22.2, R23.2

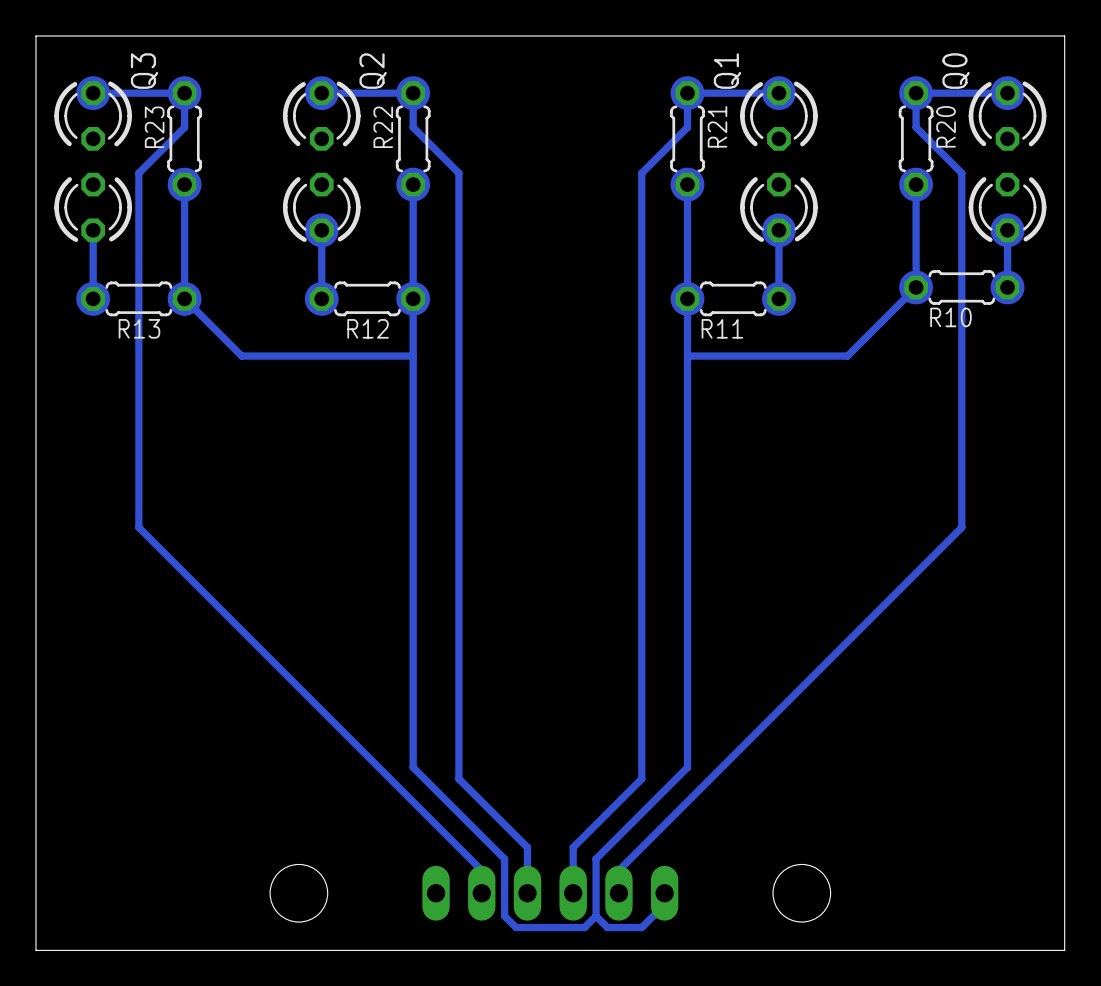
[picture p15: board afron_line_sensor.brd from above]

Board: 2 copper layers, 57.1 x 50.8 mm, 17 parts (1 on the bottom side), 10 nets.

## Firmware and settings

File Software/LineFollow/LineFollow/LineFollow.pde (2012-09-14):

/*
  Line Following Demonstration Software
  Bot Thoughts

  AFRON "10 Dollar Robotic Challenge" 

  This is the code used in the demonstration video  
 */
 
#include <Servo.h>

#define STEER 4
#define LED 13

#define THRESH 60
#define Delta_S 40
#define SCENTER 1500
#define SMIN 1050
#define SMAX 1950

Servo steer;
int s;

void setup() {                
  // initialize the digital pin as an output.
  // Pin 13 has an LED connected on most Arduino boards:
  pinMode(LED, OUTPUT);   

  Serial.begin(9600);
  Serial.println("Hello");

  motorInit();
  
  steer.attach(STEER);
  s = SCENTER;
  motorSpeed(35);
  
}

void loop() {
  int lsense, rsense;

  rsense = analogRead(0);
  lsense = analogRead(2);

  if ( lsense > THRESH && rsense > THRESH ) {
  } else if ( lsense > THRESH) {
    digitalWrite(LED, HIGH);   // set the LED on
    if ( s > SMIN) s -= Delta_S;
  } else if ( rsense > THRESH) {
    digitalWrite(LED, HIGH);   // set the LED on
    if (s < SMAX) s += Delta_S;
  } else {
    digitalWrite(LED, LOW);    // set the LED off
    if ( s < SCENTER) s += Delta_S;
    if ( s > SCENTER) s -= Delta_S;
  }
  
  steer.write(s);
  delay(20);

  /*
  Serial.print(lsense);
  Serial.print(" ");
  Serial.print(rsense);
  Serial.println();
  */
}

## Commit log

2012-09-14 Initial revision
    [AFRON_328_chassis.skp, SafeOperatingArea.ods, afron_atmega328.brd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]
2021-02-11 added missing software and documents
    [NotesBOM.ods, TenBuckBot_BOM.ods]

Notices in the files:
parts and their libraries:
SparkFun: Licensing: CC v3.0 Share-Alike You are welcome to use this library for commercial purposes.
